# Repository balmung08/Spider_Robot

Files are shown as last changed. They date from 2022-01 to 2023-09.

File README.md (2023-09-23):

# 基于树莓派的六足机器人方案设计
## 工程内容说明
* 完整工程在 https://github.com/JLU-Automation-Team/spider-robot ，增加了遥控器的micropython代码和运控相关知识概述
### hardware为项目相关硬件设计

 * 机械结构为六足机器人的3d建模工程，包括本体和云台<br>
 *  遥控器在ESP32最小开发板上集成了MPU6050和OLED接口并设计了使能引脚，可以选择是否收发外设数据
<br>文件包括PCB的立创EDA文件、Altium文件与3d模型<br>
### code文件夹内为使用到的各种代码

 * 包括pc控制的上位机和图传程序及其服务器程序、体感遥控器的驱动程序和树莓派部分执行程序
### resource文件夹为项目相关的资料

 * 包括舵机控制板的串口控制指令说明以及运动控制理论及相关资料
### software为使用到的软件内容

 * 舵机控制板的图形化编程上位机以及可能使用到的串口驱动
## 简单预览

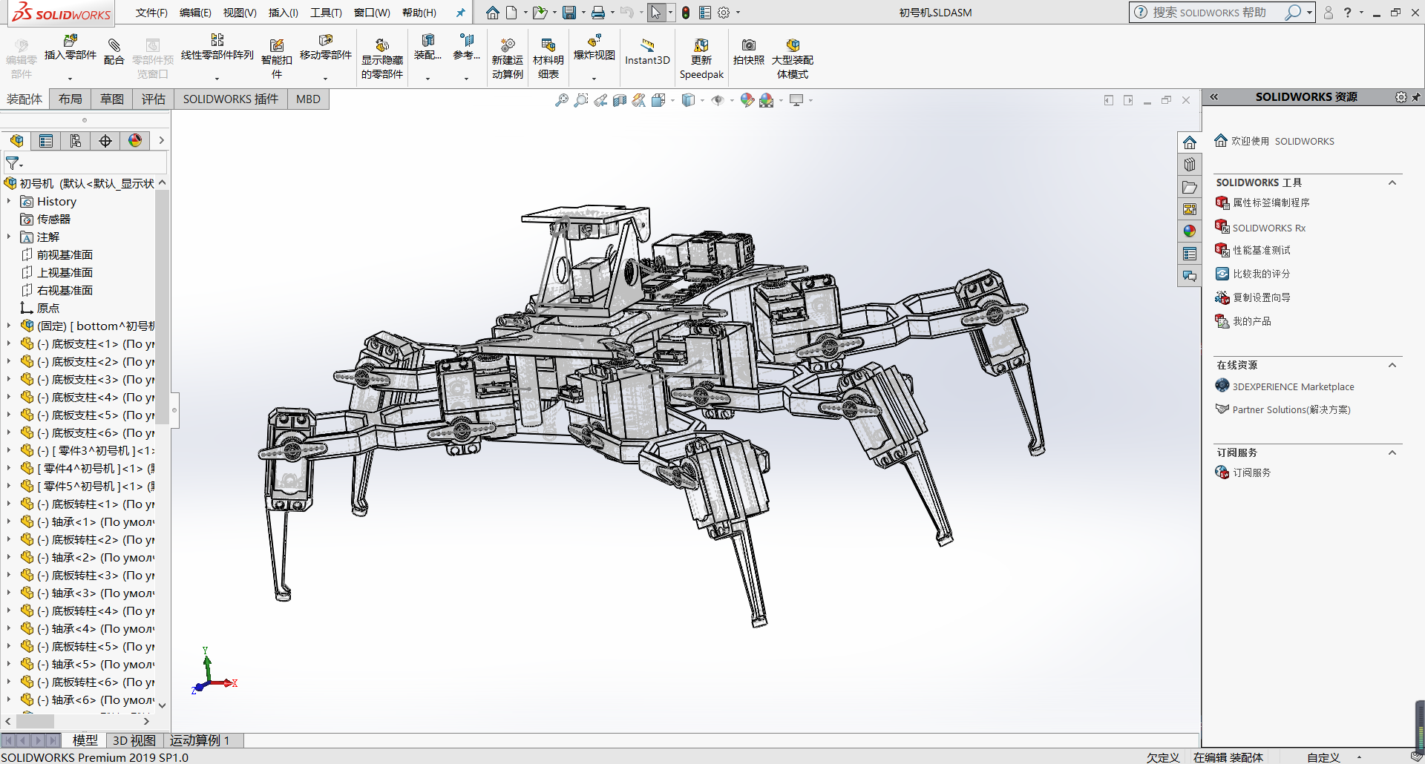
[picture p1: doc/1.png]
<br>
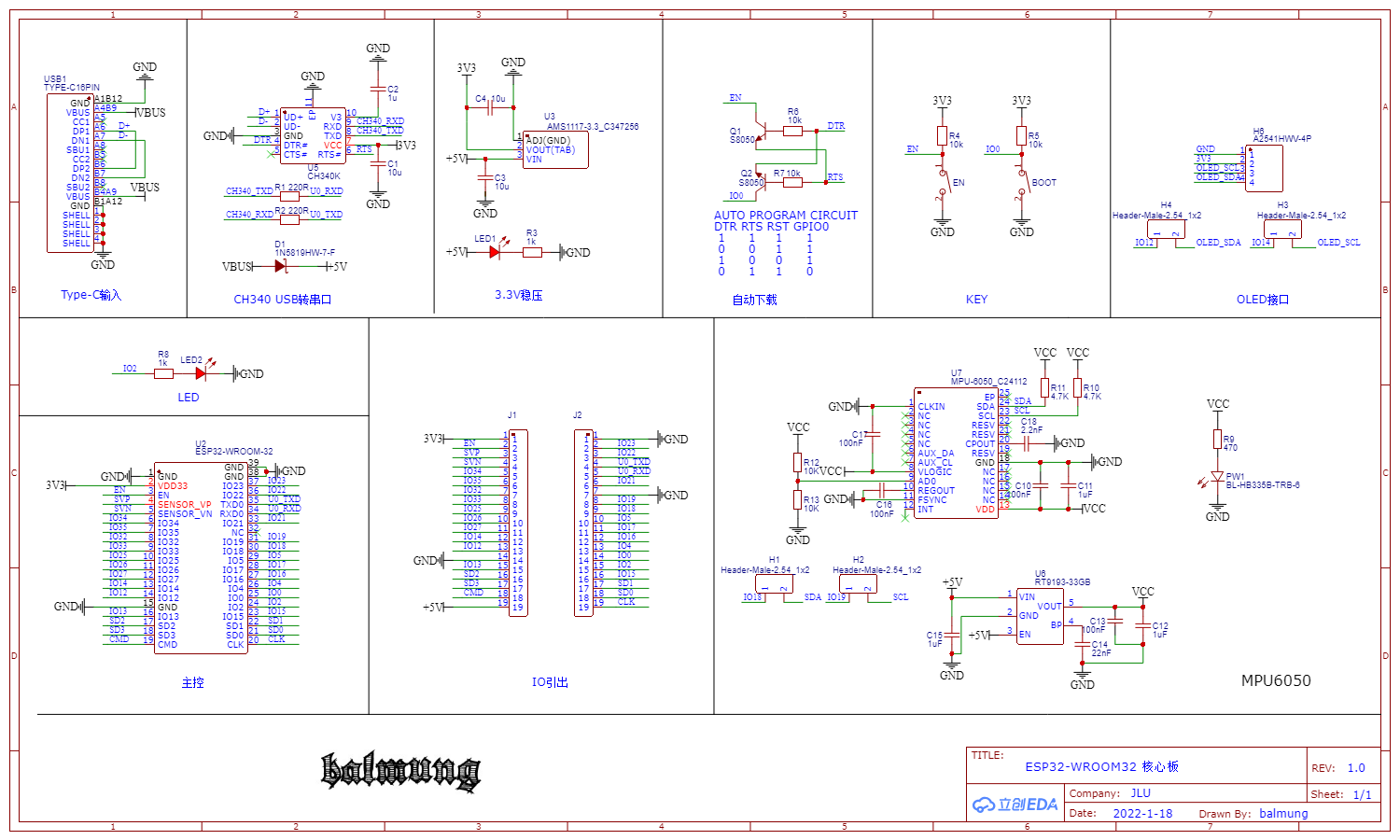
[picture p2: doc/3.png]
<br>
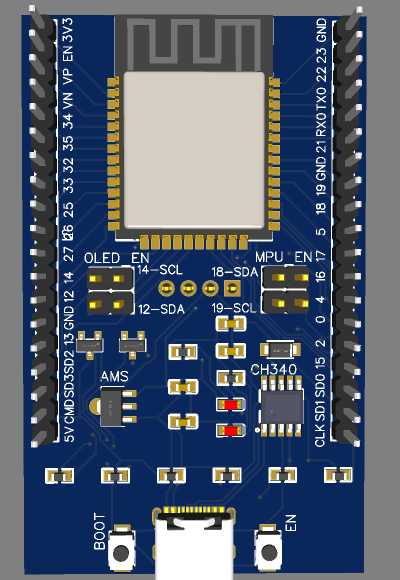
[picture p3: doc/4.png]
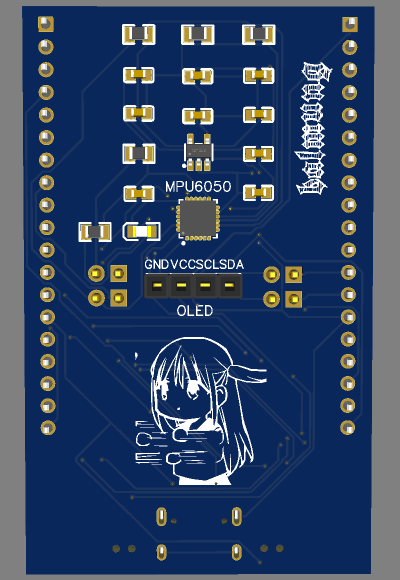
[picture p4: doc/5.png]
<br>
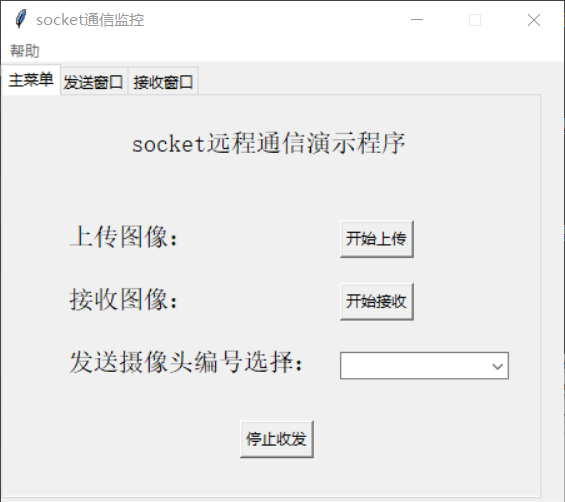
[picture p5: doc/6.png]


## 参考与致谢

>此项目在设计中参考了https://grabcad.com/library/spider-robot-v2-0-mg995-servo-quadruped-on-stm32f103-1
感谢这帮俄国佬；另外，立创EDA永远的神，我认为大家都应该试一试.jpg

>因为马上就要考研了，我们没有时间将设计做成实物，但是在设计过程中仍旧有很大收获
感谢愿意陪着我一起抽风做这玩意的两位队友: [BH3GEI](https://github.com/BH3GEI),[Panzer-Crow](https://github.com/Panzer-Crow)
------------------------
## 最终补充（addition）
> 此项目最终被本人稍作修改当成毕业设计交差了，最后主要进行了如下改动：
* 将遥控器的PCB简化为以ESP32开发板为主，仅外接OLED屏幕及按键
* 服务器端最终采用阿里云服务器，可以通过公网IP进行中转
* 在机器人上增加了JY901B进行姿态感知
* 将图传的方式由TCP改为UDP
* 之前的结构件打印后PLC强度不太够，重新从网上找了一套结构件并重新设计了适配树莓派孔位的顶板结构件
* 丰富了功能（视觉部分和动作组）
* **把论文放进了补充文档中作为参考，可对具体实现原理进行了解**
> 部分代码因为毕业了玩太爽了遗失了，对此说明如下：
* 机器人的UDP图传代码丢失，从老版本的代码修改通信方式TCP为UDP即可
* 机器人的IMU代码丢失，可以从维特智能的JY901B官网进行获取
* 上位机的图传和遥控代码均丢失……图传同上，遥控仅通过标志位进行传输，很好写
* ~~东西丢的实在太多了，有些代码也不是最终版，但是就这样算了，看看文章意思意思得了~~

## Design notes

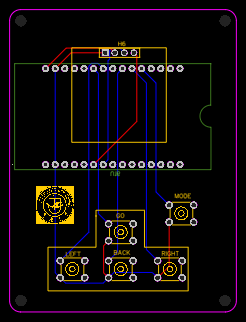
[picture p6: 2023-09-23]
addition/遥控器端/ESP32直插最简PCB.png

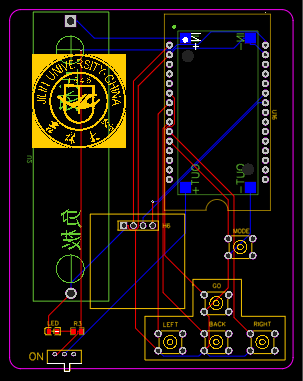
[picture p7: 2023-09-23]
addition/遥控器端/带供电PCB.png

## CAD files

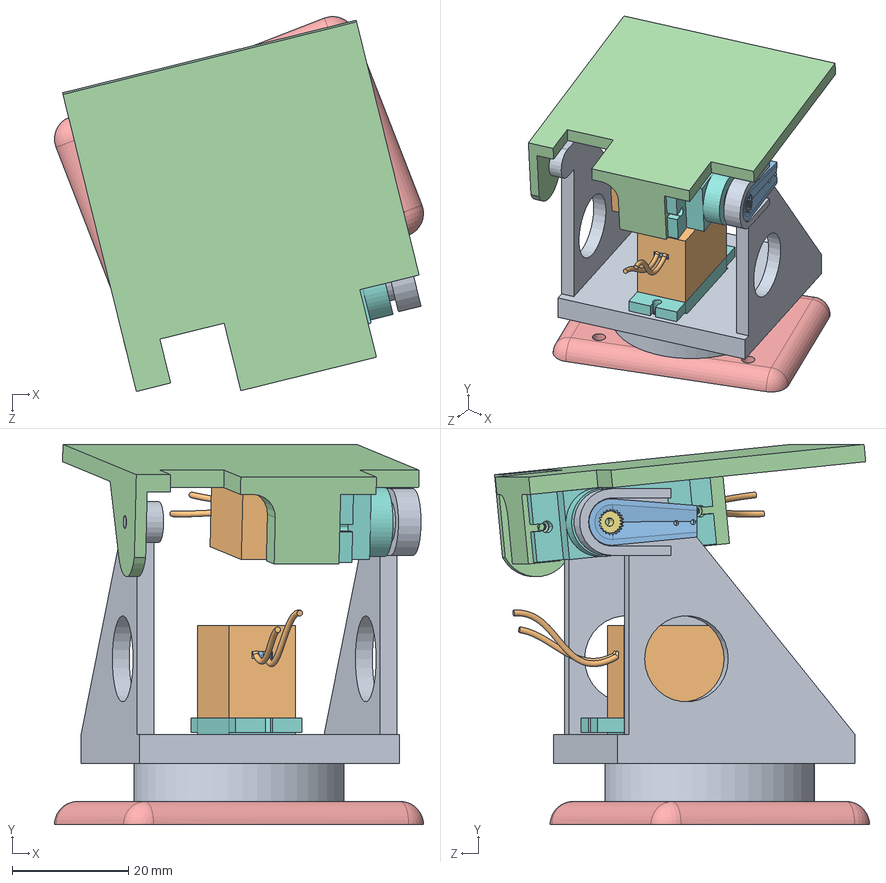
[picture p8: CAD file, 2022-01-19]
hardware/云台/云台2号机 .SLDASM
63.4 x 65.3 x 64.4 mm
云台2
lower cover^servo motor assembley(2)_servo motor assembley x 2
motor^servo motor assembley(2)_servo motor assembley x 2
feedback potentiometer^servo motor assembley(2)_servo motor assembley x 2
复件 (2) ^servo motor assembley(2)_servo motor assembley x 2
复件 (3) ^servo motor assembley(2)_servo motor assembley x 2
复件 (4) ^servo motor assembley(2)_servo motor assembley x 2
upper cover^servo motor assembley(2)_servo motor assembley x 2
复件 (6) ^servo motor assembley(2)_servo motor assembley x 2
复件 (7) ^servo motor assembley(2)_servo motor assembley x 2
舵机配件1 x 2
云台3
云台1

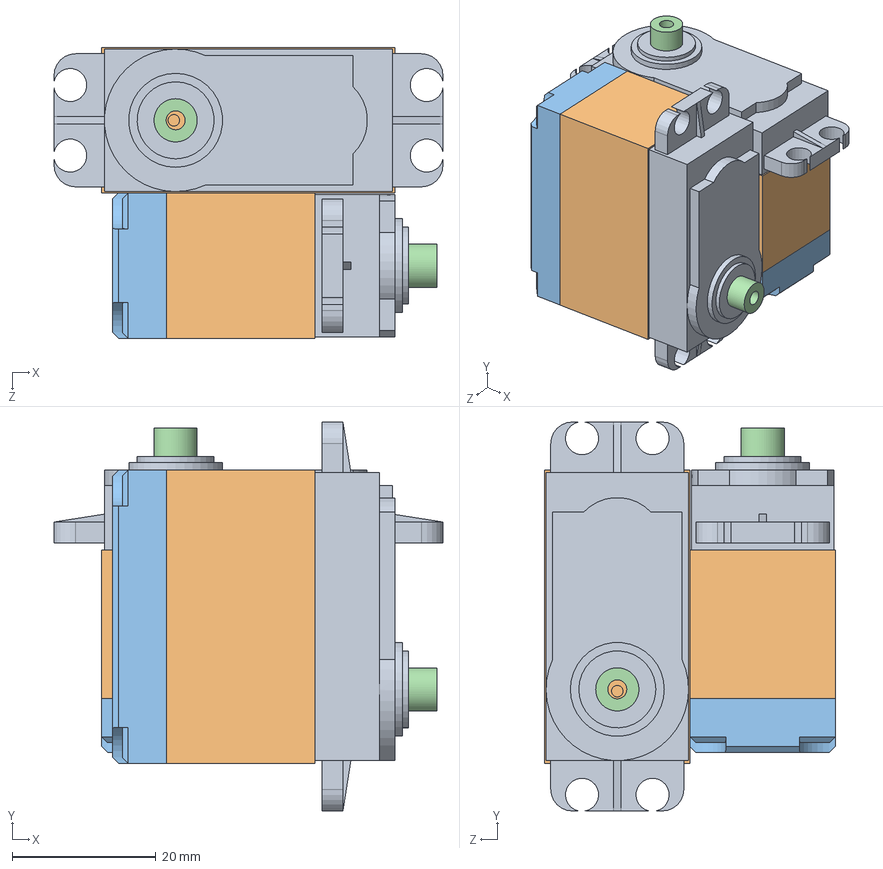
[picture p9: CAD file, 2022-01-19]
hardware/机械结构/装配体1.SLDASM
54.0 x 54.0 x 40.4 mm
MG995前板 x 2
MG995中板 x 2
MG995后板 x 2
MG995齿轮 x 2

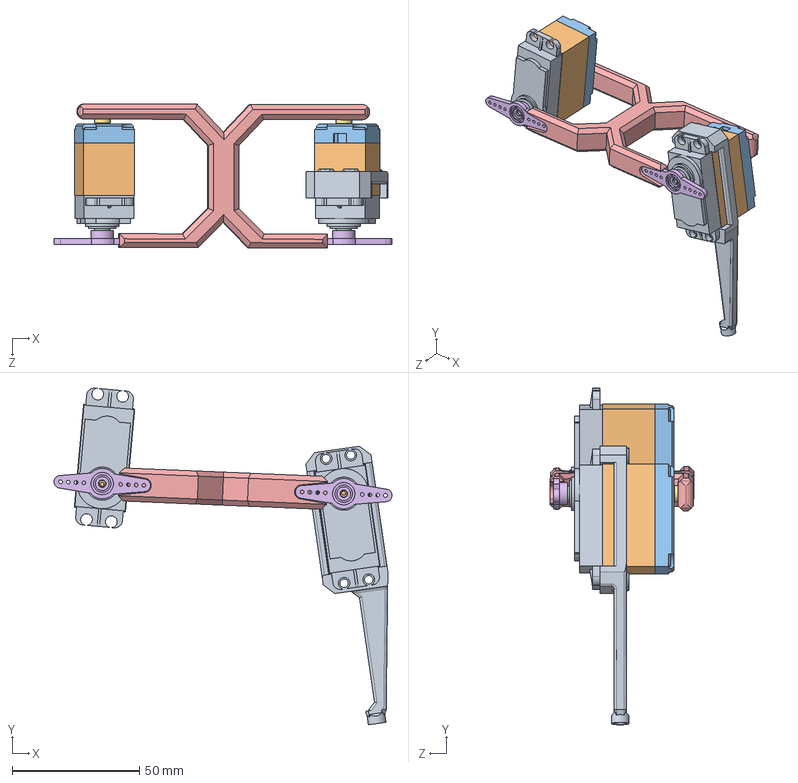
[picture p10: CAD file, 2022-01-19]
hardware/机械结构/腿2.SLDASM
133.0 x 132.5 x 56.8 mm
MG995前板 x 2
MG995中板 x 2
MG995后板 x 2
MG995齿轮 x 2
腿上部
舵机配件 x 2
腿部转柱 x 2
轴承 x 2
腿2下部

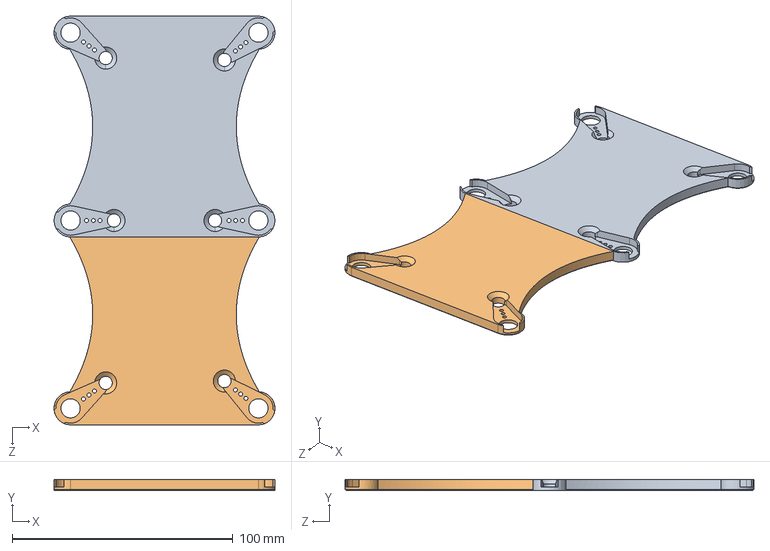
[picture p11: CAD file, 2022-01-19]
hardware/机械结构/top(3).SLDASM
100.0 x 5.00 x 185.0 mm
Основание нижнее^_top(3)_top(3)
_private_var_mobile_Containers_Data_Application_327FD876-EF9E-4CCE-9D75-9D16AF0753A7_tmp_B33AE067-E3AF-4F21-8502-7502B160869B.tmp(2)^top(3)_top(3)

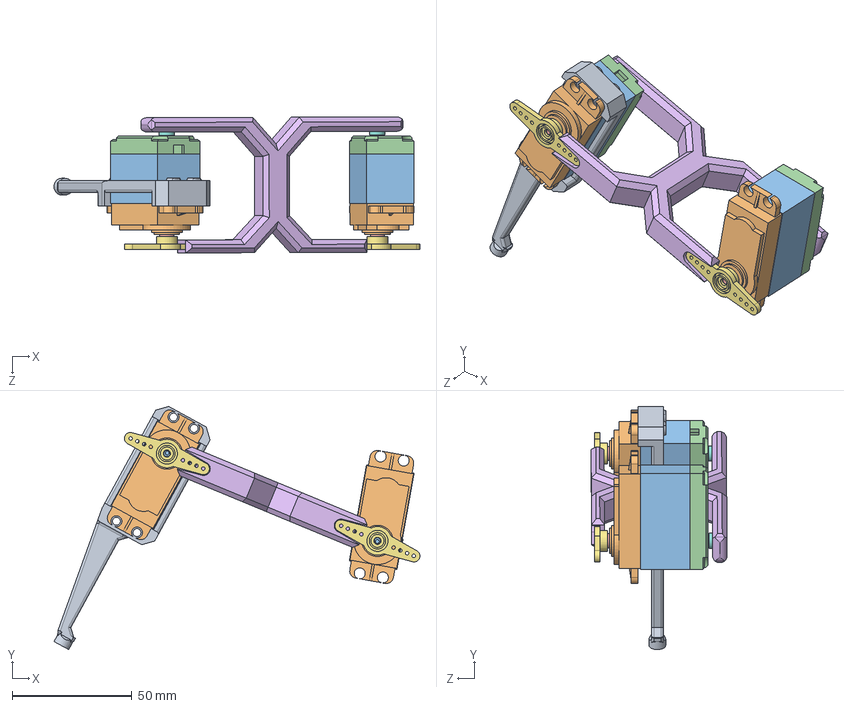
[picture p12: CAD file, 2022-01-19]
hardware/机械结构/腿1.SLDASM
152.7 x 101.4 x 56.8 mm
腿1下部
MG995前板 x 2
MG995中板 x 2
MG995后板 x 2
MG995齿轮 x 2
腿上部
舵机配件 x 2
腿部转柱 x 2
轴承 x 2

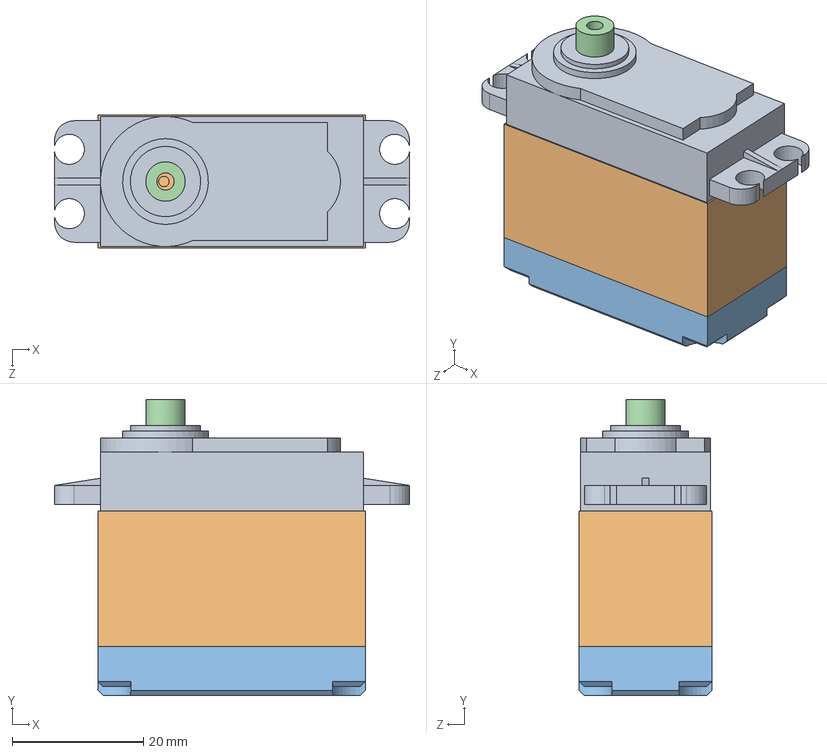
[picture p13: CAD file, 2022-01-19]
hardware/机械结构/Servo MG955.SLDASM
54.0 x 45.1 x 20.2 mm
MG995前板
MG995中板
MG995后板
MG995齿轮

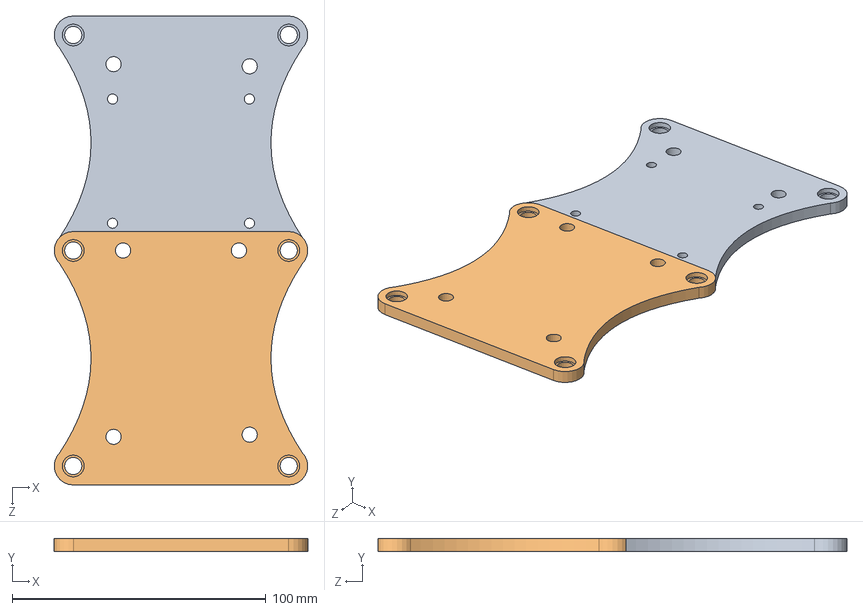
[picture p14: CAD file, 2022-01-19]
hardware/机械结构/bottom^666.SLDASM
100.0 x 5.00 x 185.0 mm
Основание нижнее.SLDPRT^bottom_666
Основание нижнее.SLDPRT-0^bottom_666

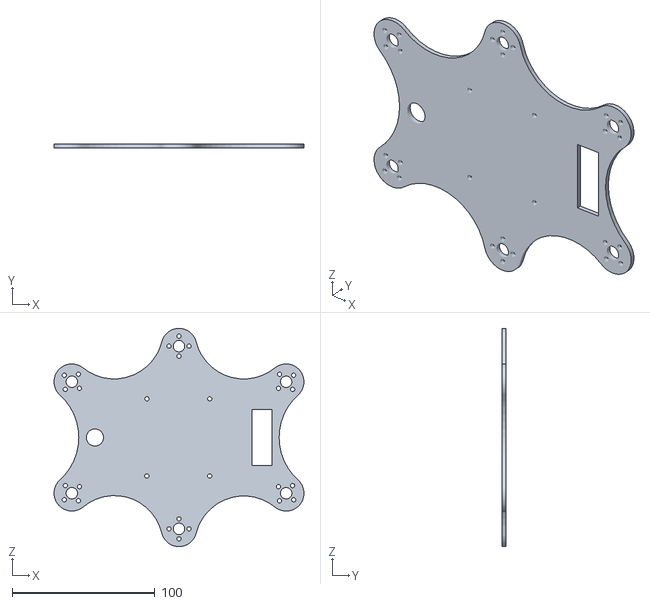
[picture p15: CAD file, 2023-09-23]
addition/机器人端/结构件设计/结构件/零件1（适配树莓派开孔顶板）.STL
175.0 x 2.50 x 152.8

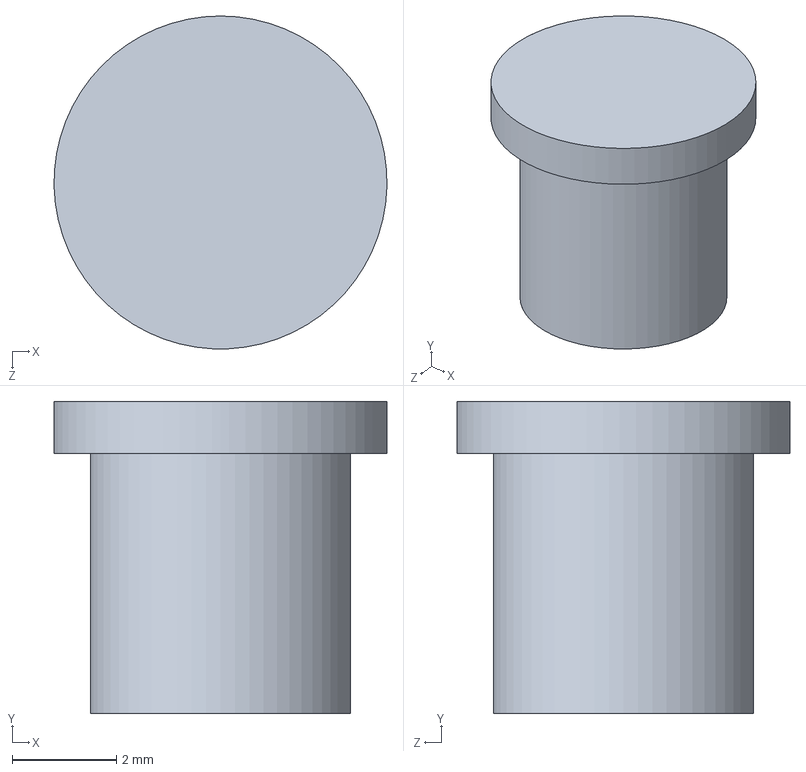
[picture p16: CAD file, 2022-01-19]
hardware/机械结构/底板转柱.SLDPRT
6.40 x 6.00 x 6.40 mm

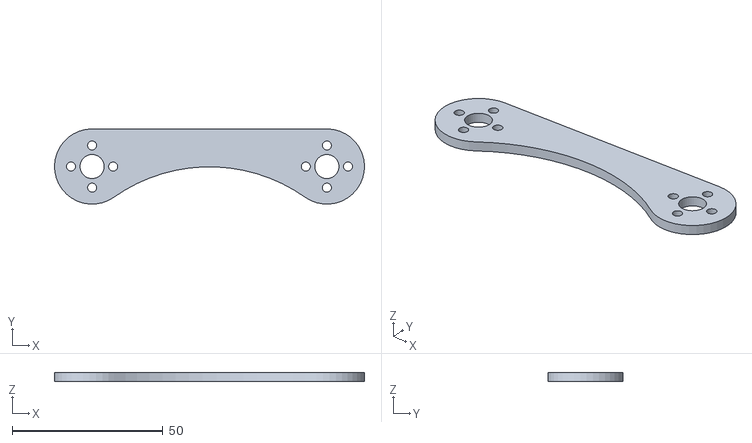
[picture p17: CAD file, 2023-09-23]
addition/机器人端/结构件设计/结构件/小腿.STL
103.0 x 25.0 x 3.00

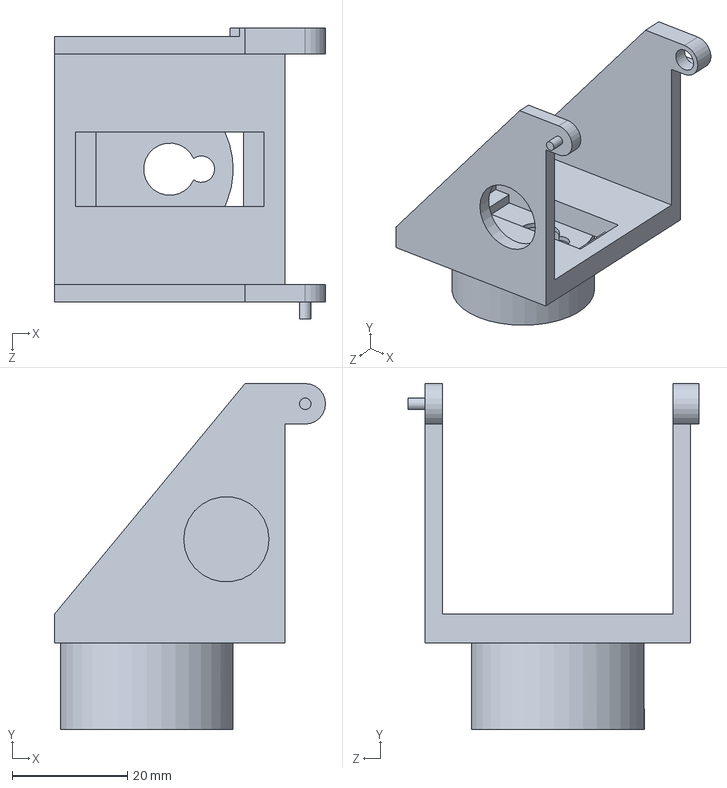
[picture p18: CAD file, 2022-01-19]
hardware/云台/云台2.SLDPRT
47.0 x 60.0 x 50.5 mm

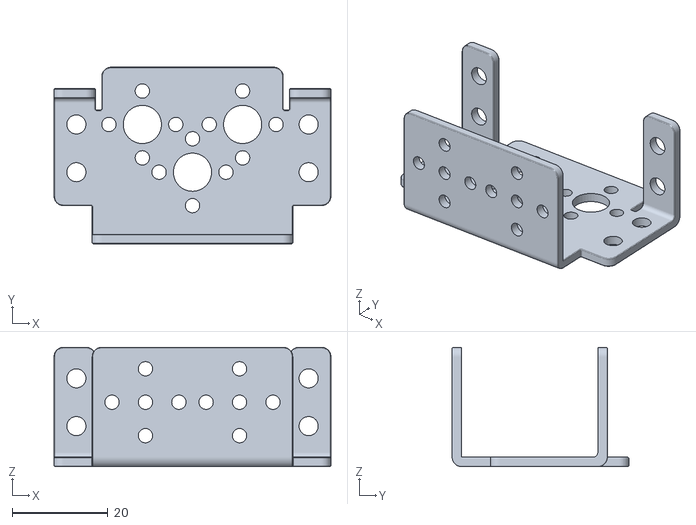
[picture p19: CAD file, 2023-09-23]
addition/机器人端/结构件设计/结构件/多功能支架.STL
58.0 x 37.0 x 25.0

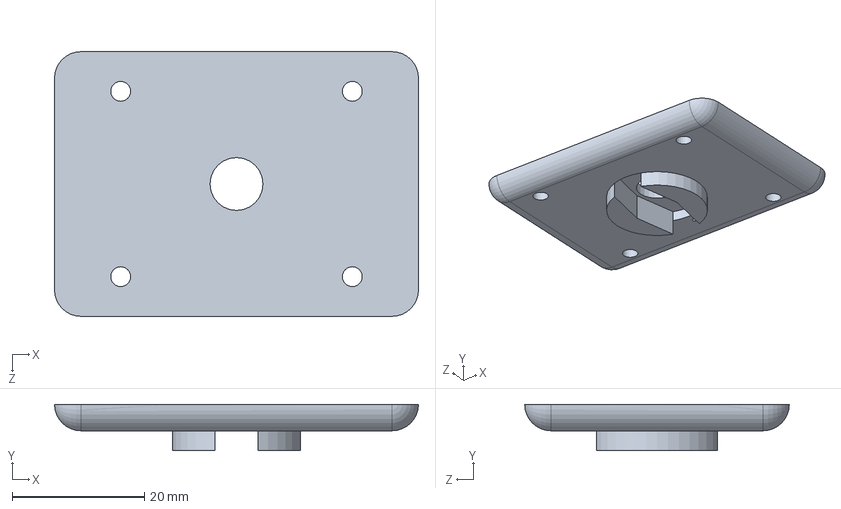
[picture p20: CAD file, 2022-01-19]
hardware/云台/云台1.SLDPRT
55.0 x 7.00 x 40.0 mm

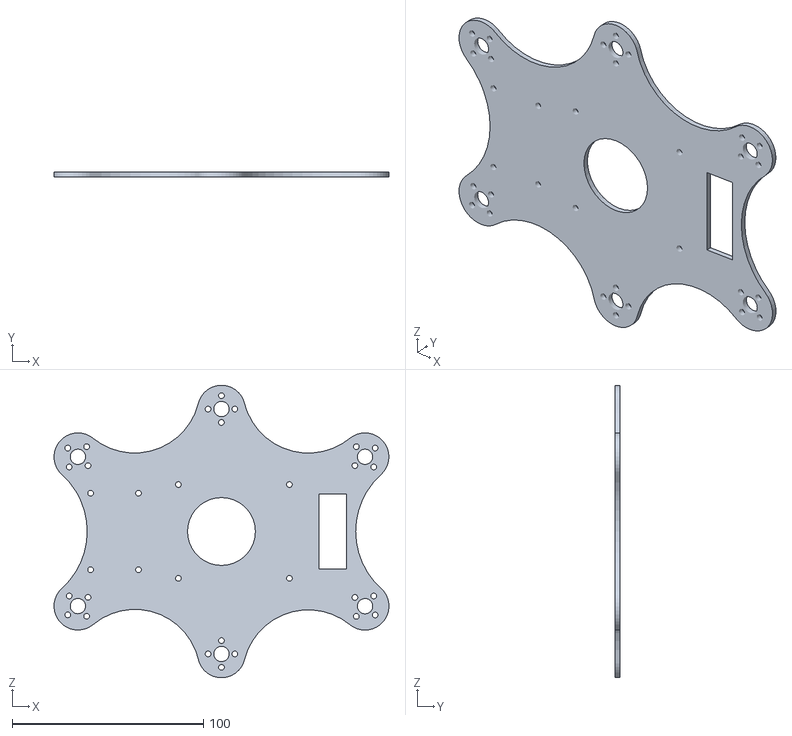
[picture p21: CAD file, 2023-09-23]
addition/机器人端/结构件设计/结构件/零件2（适配树莓派开孔顶板2）.STL
175.0 x 2.50 x 152.8

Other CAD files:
hardware/机械结构/镜向固定件2.sldprt
hardware/云台/舵机配件1.SLDPRT
hardware/机械结构/固定件2.sldprt
addition/机器人端/结构件设计/结构件/舵机.STL
addition/机器人端/结构件设计/结构件/上盖板.STL
addition/机器人端/结构件设计/结构件/下盖板.STL
addition/机器人端/结构件设计/结构件/大腿.STL
addition/机器人端/结构件设计/结构件/金属舵盘.STL
hardware/云台/云台3.SLDPRT
hardware/机械结构/MG995中板.SLDPRT
hardware/机械结构/MG995前板.SLDPRT
hardware/机械结构/MG995后板.SLDPRT
hardware/机械结构/MG995齿轮.SLDPRT
hardware/机械结构/固定件1.sldprt
hardware/机械结构/底板支柱.SLDPRT
hardware/机械结构/腿1下部.SLDPRT
hardware/机械结构/腿2下部.SLDPRT
hardware/机械结构/腿上部.SLDPRT
hardware/机械结构/腿部转柱.SLDPRT
hardware/机械结构/舵机配件.SLDPRT
hardware/机械结构/舵机驱动板示意图.SLDPRT
hardware/机械结构/轴承.SLDPRT
hardware/机械结构/镜向固定件1.sldprt

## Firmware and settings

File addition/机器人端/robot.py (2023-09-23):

import time
import RPi.GPIO as GPIO
import serial
import socket
import pigpio
import cv2
import visual
import imu

def read_code():
    def connect():
        # HOST = 'localhost'
        HOST = '8.130.72.154'  # 服务器的公网IP
        PORT = 1178
        sock = socket.socket(socket.AF_INET, socket.SOCK_STREAM)
        sock.setsockopt(socket.SOL_SOCKET, socket.SO_REUSEADDR, 1)
        sock.connect((HOST, PORT))
        return sock
    def read_target():
        sock.send("do".encode())
        status = sock.recv(1).decode()
        return status
    def read_mode():
        sock.send("mo".encode())
        status = sock.recv(1).decode()
        return status
    '''
    def read_mode():
        sock.send("mo".encode())
        status = sock.recv(1).decode()
        return status
    '''
    sock = connect()
    status = read_target()
    sock = connect()
    mode = read_mode()
    #print("status:" + str(status))
    return status,mode
def send_code(code):
    def connect():
        # HOST = 'localhost'
        HOST = '8.130.72.154'  # 服务器的公网IP
        PORT = 1177
        sock = socket.socket(socket.AF_INET, socket.SOCK_STREAM)
        sock.setsockopt(socket.SOL_SOCKET, socket.SO_REUSEADDR, 1)
        sock.connect((HOST, PORT))
        return sock

    def update(data):
        sock.send("up".encode())
        sock.send(str(data).encode())
    sock = connect()
    update(code)
    print("sending:"+ str(code))

def go_straight():
    init_angle = imu.return_z()
    print("init_angle:"+str(init_angle))
    #st = b'UU\x05\x06\x01\x01\x00'
    fin = b'UU\x05\x08\x01\x01\x00'
    start = "55 55 05 06 00 01 00"
    left = "55 55 05 06 03 01 00"
    right = "55 55 05 06 04 01 00"
    straight = "55 55 05 06 01 01 00"
    small_right = "55 55 05 06 06 01 00"
    small_left = "55 55 05 06 07 01 00"
    mov = 1
    i = 1
    while True:
        if i==3:
            init_angle = imu.return_z()
        print(imu.return_z())
        err_angle = imu.return_z()-init_angle
        #print(imu.return_z())
        print("err:"+ str(err_angle))
        if -5 <= err_angle and err_angle <= 5:
            ted.write(bytes.fromhex(straight))
            ted.read(14)
            mov = 0
            '''
            if ted.read(7) == fin:
                mov = 0
                print("fin")
            '''
        err_angle = imu.return_z()-init_angle
        if err_angle>= 5:
            ted.write(bytes.fromhex(small_right))
            ted.read(14)
            print('turn right!')
        if err_angle <= -5:
            ted.write(bytes.fromhex(small_left))
            ted.read(14)
            print('turn left!')
        if str(read_code()[0]) != "1":
            #print(str(read_code()))
            print("exit_straight")
            break
        i += 1
        

    #print(imu.return_z())
ted = serial.Serial(port="/dev/ttyAMA1", baudrate=9600)
start = "55 55 05 06 00 01 00"
straight = "55 55 05 06 01 01 00"
back = "55 55 05 06 02 01 00"
left = "55 55 05 06 03 01 00"
right = "55 55 05 06 04 01 00"
small_left = "55 55 05 06 06 01 00"
small_right = "55 55 05 06 07 01 00"
servo1 = 78
servo2 = 20
# PWM1:2-13
GPIO.setmode(GPIO.BCM)
servo_pwm1 = pigpio.pi()
servo_pwm1.set_PWM_frequency(18,50)
servo_pwm1.set_PWM_range(18,1000)

servo_pwm2 = pigpio.pi()
servo_pwm2.set_PWM_frequency(23,50)
servo_pwm2.set_PWM_range(23,1000)

servo_pwm1.set_PWM_dutycycle(18,78)
servo_pwm2.set_PWM_dutycycle(23,20)
time_old = time.time()
video = cv2.VideoCapture(0)
mode = "0"
target = "0"



while True:
    if mode == "0":
        try:
            while True:
                status,mode = read_code()
                print(status,mode)
                if mode != "0":
                    print("out")
                    break
                if status == "0":
                    ted.write(bytes.fromhex(start))
                    time.sleep(0.05)
                if status == "1" :
                    print(2222)
                    go_straight()
                    #ted.write(bytes.fromhex(straight))
                    time.sleep(0.05)
                if status == "2" :
                    ted.write(bytes.fromhex(left))
                    time.sleep(0.05)
                if status == "3" :
                    ted.write(bytes.fromhex(back))
                    time.sleep(0.05)
                if status == "4" :
                    ted.write(bytes.fromhex(right))
                    time.sleep(0.05)
                if status == "5" :
                    if time.time()-time_old>0:
                        servo2 = servo2+10
                        if servo2 <= 25:
                            servo2 = 25
                        servo_pwm2.set_PWM_dutycycle(23,servo2)
                        time_old = time.time()
                        send_code(0)
                if status == "6" :
                    if time.time()-time_old>0.1:
                        servo2 = servo2-10
                        if servo2 >= 250:
                            servo2 = 250
                        servo_pwm2.set_PWM_dutycycle(23,servo2)
                        time_old = time.time()
                        send_code(0)
                if status == "7" :
                    if time.time()-time_old>0.1:
                        servo1 = servo1+10
                        if servo1 >= 125:
                            servo1 = 125
                        servo_pwm1.set_PWM_dutycycle(18,servo1)
                        time_old = time.time()
                        send_code(0)
                if status == "8" :
                    if time.time()-time_old>0.1:
                        servo1 = servo1-10
                        if servo1 <= 25:
                            servo1 = 25
                        servo_pwm1.set_PWM_dutycycle(18,servo1)
                        time_old = time.time()
                        send_code(0)
                print("fin")
        except Exception as e:
            print(e)
            time.sleep(1)
    if mode == "1":
        target = status
        if target == "1" or target == "2":
            s,x,y,w,h = visual.detect(int(target),video)
        if target == "0":
            s,x,y,r = visual.detect(int(target),video)
        print("doing:"+str(x))
        if s==1:
            if x>=1 and x<=240:
                ted.write(bytes.fromhex(small_right))
                #print("l")
                time.sleep(0.05)
            if x>=400:
                ted.write(bytes.fromhex(small_left))
                #print("r")
                time.sleep(0.05)
            if 240<x<400:
                ted.write(bytes.fromhex(start))
        if s==0:
            print("no")
            ted.write(bytes.fromhex(start))
            time.sleep(0.05)

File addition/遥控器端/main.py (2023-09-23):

# 连接wifi，将IP地址等相关信息通过OLED显示（只支持2.4G网络）。
import network,time
from machine import I2C,Pin,ADC,PWM
from ssd1306 import SSD1306_I2C
import _thread
import random
import network,socket

#WIFI连接函数
def WIFI_Connect():
    global status
    WIFI_LED=Pin(2, Pin.OUT) #初始化WIFI指示灯
    wlan = network.WLAN(network.STA_IF) #STA模式
    wlan.active(False)
    time.sleep(1)
    wlan.active(True)                   #激活接口
    start_time=time.time()              #记录时间做超时判断
    print("connect_start")
    while not wlan.isconnected():
        try:
            wlan.active(True)
            wlan.connect('BALMUNG 9685', 'balmung08') #输入WIFI账号密码
            print("doing")
        except Exception as e:
            print(e)
            while not wlan.isconnected():
                print("trying")
                wlan.active(True)
                #wlan.active(False) 
                WIFI_LED.value(1)
                time.sleep_ms(50)
                WIFI_LED.value(0)
                time.sleep_ms(50)
                if time.time()-start_time > 5 :
                    oled.fill(0)   #清屏背景黑色
                    oled.text('internet:defeat',0,0)
                    oled.show()
                    print("defeat")
                break
    if wlan.isconnected():
        print("WLAN_SUCCESS")
        WIFI_LED.value(1)
        oled.fill(0)   #清屏背景黑色
        oled.text('internet:connect',0,0)
        oled.text('status:0', 0, 15)
        oled.text('mode:0',0,30)
        oled.show()
def send_code(code):
    s=socket.socket(socket.AF_INET,socket.SOCK_STREAM)
    addr=('8.130.72.154',1177) #服务器IP和端口
    s.setsockopt(socket.SOL_SOCKET, socket.SO_REUSEADDR, 1)   #设置套接字
    s.connect(addr)
    s.send('up')
    s.send(str(code))
    return s
def send_mode(mode):
    s=socket.socket(socket.AF_INET,socket.SOCK_STREAM)
    addr=('8.130.72.154',1177) #服务器IP和端口
    s.setsockopt(socket.SOL_SOCKET, socket.SO_REUSEADDR, 1)   #设置套接字
    s.connect(addr)
    s.send('mp')
    s.send(str(mode))
    return s
if __name__ == '__main__':
    KEY1=Pin(16,Pin.IN,Pin.PULL_UP) #构建 KEY 对象
    KEY2=Pin(17,Pin.IN,Pin.PULL_UP) #构建 KEY 对象
    KEY3=Pin(18,Pin.IN,Pin.PULL_UP) #构建 KEY 对象
    KEY4=Pin(19,Pin.IN,Pin.PULL_UP) #构建 KEY 对象
    KEY5=Pin(21,Pin.IN,Pin.PULL_UP) #构建 KEY 对象
    state=0 #LED 引脚状态
    i2c = I2C(sda=Pin(27), scl=Pin(26))   #I2C初始化：sda--> 13, scl --> 14
    oled = SSD1306_I2C(128, 64, i2c, addr=0x3c) #OLED显示屏初始化：128*64分辨率,OLED的I2C地址是0x3c
    count = 0
    mode = 0
    print("init_success")
    WIFI_Connect()
    print("connect_success")
    mode_sw = 0
    target = 1
    while True:
        status = 0
        if KEY1.value()==0: #按键被按下
            time.sleep_ms(10) #消除抖动
            if KEY1.value()==0: #确认按键被按下
                if mode == 0:
                    status = 1
                    s = send_code(1)
                    s.close()
                    print(1)
                oled.fill(0)
                oled.text('internet:connect',0,0)
                if mode == 0:
                    oled.text('status:1',0,15)
                    oled.text('target:---',0,45)
                if mode == 1:
                    oled.text('status:---',0,15)
                    oled.text('target:'+str(target),0,45)
                oled.text('mode:'+str(mode),0,30)
                oled.show()   #OLED执行显示
        if KEY2.value()==0: #按键被按下
            time.sleep_ms(10) #消除抖动
            if KEY2.value()==0: #确认按键被按下
                if mode == 0:
                    status = 2
                    oled.fill(0)
                    s= send_code(2)
                    s.close()
                    print(2)
                oled.text('internet:connect',0,0)
                if mode == 0:
                    oled.text('status:2',0,15)
                    oled.text('target:---',0,45)
                if mode == 1:
                    oled.text('status:---',0,15)
                    oled.text('target:'+str(target),0,45)
                oled.text('mode:'+str(mode),0,30)
                oled.show()   #OLED执行显示

        if KEY3.value()==0: #按键被按下
            time.sleep_ms(10) #消除抖动
            if KEY3.value()==0: #确认按键被按下
                if mode == 0:
                    status = 3
                    s = send_code(3)
                    s.close()
                    print(3)
                oled.fill(0)
                oled.text('internet:connect',0,0)
                if mode == 0:
                    oled.text('status:3',0,15)
                    oled.text('target:---',0,45)
                if mode == 1:
                    oled.text('status:---',0,15)
                    oled.text('target:'+str(target),0,45)
                oled.text('mode:'+str(mode),0,30)
                oled.show()   #OLED执行显示
        if KEY4.value()==0: #按键被按下
            time.sleep_ms(10) #消除抖动
            if KEY4.value()==0: #确认按键被按下
                if mode == 0:
                    status = 4
                    s = send_code(4)
                    s.close()
                    print(4)
                oled.fill(0)
                oled.text('internet:connect',0,0)
                if mode == 0:
                    oled.text('status:4',0,15)
                    oled.text('target:---',0,45)
                if mode == 1:
                    oled.text('status:---',0,15)
                    oled.text('target:'+str(target),0,45)
                oled.text('mode:'+str(mode),0,30)
                oled.show()   #OLED执行显示
        if KEY5.value()==0: #按键被按下
            time.sleep_ms(10) #消除抖动
            if KEY5.value()==0: #确认按键被按下
                print(count)
                if count == 2:
                    if mode == 1:
                        target += 1
                        if target == 3:
                            target = 0
                        s = send_code(target)
                        s.close()
                        status = 5
                        oled.fill(0)
                        oled.text('internet:connect',0,0)
                        oled.text('status:---',0,15)
                        oled.text('mode:'+str(mode),0,30)
                        oled.text('target:'+str(target),0,45)
                        oled.show()   #OLED执行显示
                if count==7:
                    mode = int(not(mode))
                    s = send_mode(mode)
                    s.close()
                count+=1

        else:
            count = 0
            mode_sw = 0
        if status==0:
            if mode == 0:
                s = send_code(0)
                s.close()
                s = send_mode(0)
                s.close()
            oled.fill(0)
            oled.text('internet:connect',0,0)
            if mode == 0:
                oled.text('status:0',0,15)
                oled.text('target:---',0,45)
            if mode == 1:
                oled.text('status:---',0,15)
                oled.text('target:'+str(target),0,45)
            oled.text('mode:'+str(mode),0,30)
            oled.show()
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
